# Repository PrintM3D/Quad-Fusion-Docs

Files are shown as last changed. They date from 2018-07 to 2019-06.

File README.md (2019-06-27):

# Welcome

                                                                                                                                                                                                                                                                                                                                                                                                                                                                                                                                                                                                                                                                               Welcome to the User Manual for the the QuadFusion print head.  This manual is hosted in GitHub.com and managed via GitBook.com.  Please feel free to add suggestions to any of the guides by creating a pull request or issue on [GitHub](https://github.com/PrintM3D/Quad-Fusion-Docs/issues).

NEW - July 2019 WalkThrough / Crash Course: For users setting up their quad head for the first time and looking to gain a deep understanding of the system to get the best results, start [here](https://coda.io/d/M3D-Official-Troubleshooting-Self-Help-Guide_dzE73kMbIAL/Quad-Expert-Crash-Course_sudLH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).

Steps/mm: For users setting up QuadFusion heads on their own system, important information can be found [here](getting-started/updating-control-board-settings.md).

**This user manual is a work in progress and may contain incomplete or incorrect information.  Please exercise caution with the information contained herein.  This message will be removed as the guide matures.**

If you are a complete beginner to 3D printing, please start at the [Beginner Guides](beginner-guides/).

If you are a more experienced 3D printer user, [Get Started Here](https://m3d.gitbook.io/m3d-quadfusion-documentation/getting-started).  This guide will get you set-up and walk you through your first print.

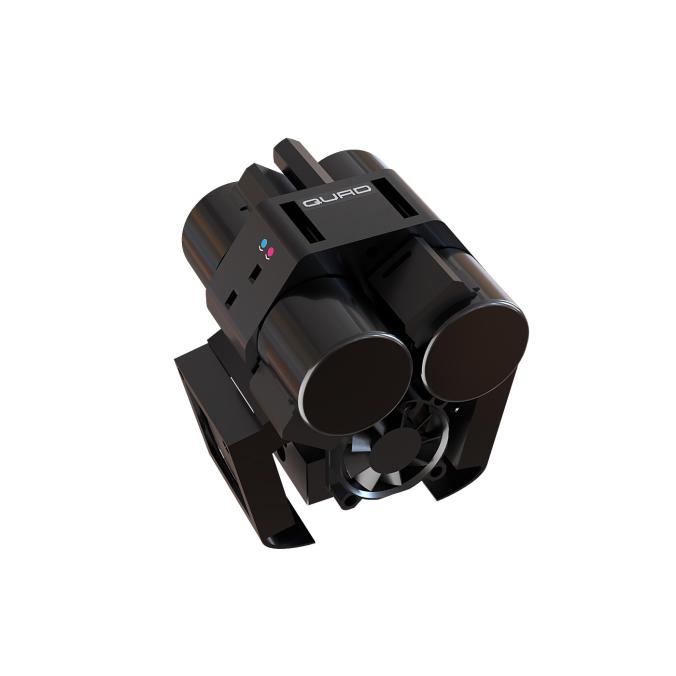
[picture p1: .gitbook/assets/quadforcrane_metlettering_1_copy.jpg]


## Contributing

The main way to collaborate to the guides is to become a collaborator.  But sometimes you simply want to submit a small contribution, without becoming a regular collaborator.

On GitHub, one can use the popular _Pull Request_ feature.  To do so, you would clone [https://github.com/PrintM3D/Quad-Fusion-Docs](https://github.com/PrintM3D/Quad-Fusion-Docs), make changes on your own copy, and submit back your changes by submitting a _Pull Request_ to M3D.  Then we will review the changes accordingly.

Thank you!

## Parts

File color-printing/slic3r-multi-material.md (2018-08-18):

# Slic3r Multi-Material

{% hint style="info" %}
Support for multi-color printing in common slicers is often limited to specific purposes or capabilities.  In this guide, we use Slic3r Prusa Edition and an M3D-developed script to make the generated G-Code compatible with a QuadFusion-enabled printer.  As slicer capabilities improve, this guide will be updated and the process will be simplified.
{% endhint %}

## You Will Need

Slic3r Prusa Edition \(link\)

NOTE: have been using 1.39.1

M3D Cleanup Script \(link\)

IPython Notebook or equivalent, such as Jupyter Notebook \(link\)

## Find \(or Create\) Multi-Part STL Set

## 

## Slice and Export

#### Load and Adjust Print Settings

#### Assign Tool Numbers

## Manual Cleanup Step

## Automated Cleanup Script

Take the .gcode file from the prior step and move it to your IPython working folder.  For example, on my system, these files are held in ~/Documents/Workspaces/\_python.  For this example, I moved the file "ed\_MAN1\_tower-of-cascades.gcode" to ~/Documents/Workspaces/\_python/Working.  \("Working" has been a convenient folder to hold the .gcode files separate from the actual IPython script file\(s\).\)

Launch IPython Notebook and load the script titled "PostprocSPEForColor4\_auto.ipynb".

Run the first three blocks of code.  \(The first is a short block defining "clamp" and nothing else; the next are much longer.\)

In the fourth code block, there is a note on values you will need to change for your particular job.  Adjust these values to your particular job.  First layer and other layer height are from your slicer setup.  The in file is the file you created in the prior step.  The out file is the .gcode file that will be created by the cleanup script and sent to the printer.

A large number of diagnostics messages will output when this code block is run.

TODO: in main -- find "def main\(\):"

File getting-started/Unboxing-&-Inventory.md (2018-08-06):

---
description: >-
  Included in the QuadFusion 3D Print Head package you will find a 3 fan mounts,
  3 fan guides, fasteners and cables. You will also find a sticker indicating
  the version shipped.
---

# Unboxing & Inventory

## Assembling the QuadFusion 3D Print Head

The QuadFusion 3D Print Head needs to be assembled before you can mount it to your printer.  Please follow these steps to complete the assembly

1. Attach the fan mounts to the QuadFusion:

    2. Attach the fan guides to the fans:

    3. Attach the fans to the fan mounts:

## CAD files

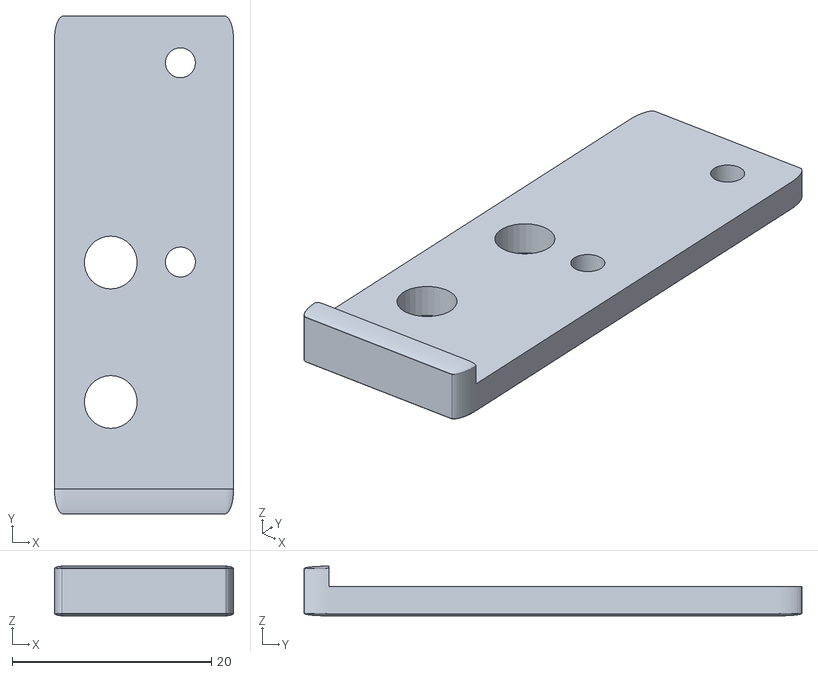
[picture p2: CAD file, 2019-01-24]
.gitbook/assets/cr10s_quad_stencil.stl
18.0 x 50.0 x 5.00

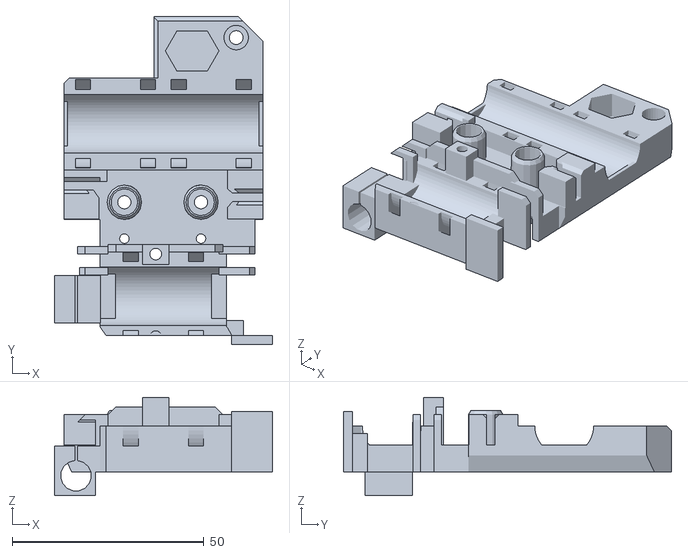
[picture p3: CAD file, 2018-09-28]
.gitbook/assets/prusa_quad_mount.STL
57.0 x 85.6 x 25.7

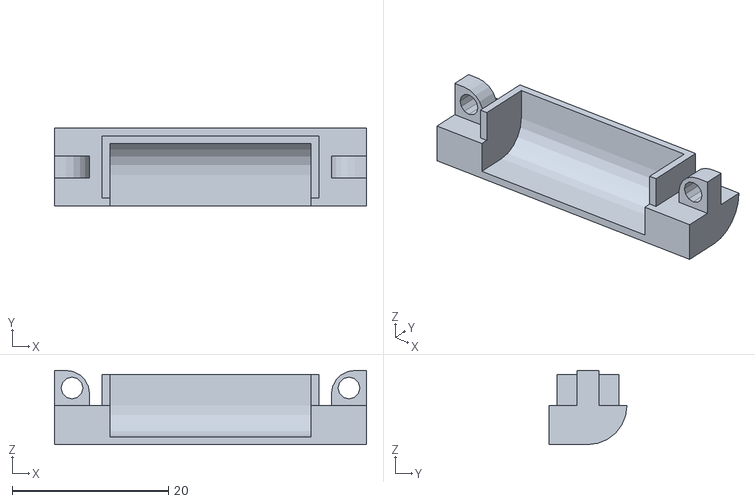
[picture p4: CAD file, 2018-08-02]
.gitbook/assets/quad-nozzle-fan-duct-v1.0.STL
40.0 x 10.0 x 9.50

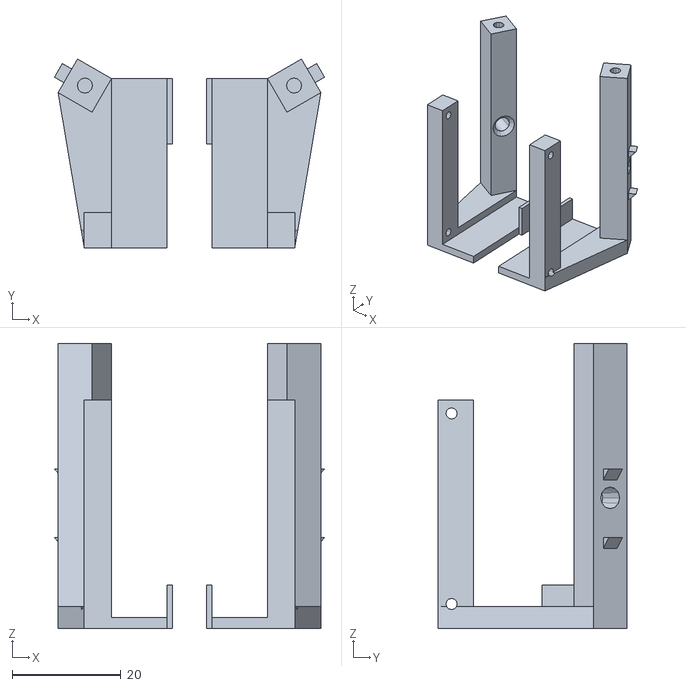
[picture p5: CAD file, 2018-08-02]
.gitbook/assets/quad-fan-mount-2-v1.1.STL
49.6 x 34.7 x 52.4

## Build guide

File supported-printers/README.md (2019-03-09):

# Printer Installation

The QuadFusion is a versatile 3D print head, so it is very likely that it will be able to adapt to whatever printer you have at home. At M3D we have mounted the QuadFusion on many different types of printers. The following guides will show you how we attached the QuadFusion not only mechanically, but electrically as well.

{% hint style="info" %}
The QuadFusion is compatible with most 3D printers, including those not listed here!
{% endhint %}

{% hint style="warning" %}
**Disclaimer: Some of the printers listed are NOT M3D products. We would like to make it clear that we have no affiliation with these printers or the companies that made them.**
{% endhint %}

{% page-ref page="m3d-crane.md" %}

{% page-ref page="m3d-promega.md" %}

{% page-ref page="cr-10s.md" %}

{% page-ref page="prusa-i3-mk2s.md" %}

{% page-ref page="duet-maestro-wiring.md" %}

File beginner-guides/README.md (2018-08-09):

# Beginner Guides

This chapter serves as an introduction to 3D printers for Quad Fusion 3D Print Head users who are not familiar with 3D printing. You will find numerous guides that explain fundamental 3D printing concepts from the start. Experienced 3D printer users are welcome too! You never know what information you might find in this chapter. If you are a more experienced 3D printer user, please follow the [Getting Started](../getting-started/) chapter.

{% page-ref page="beginner-preparation.md" %}

{% page-ref page="beginner-moving-the-motors.md" %}

{% page-ref page="beginner-introduction-to-g-code-commands.md" %}

{% page-ref page="beginner-software-layers.md" %}

{% page-ref page="beginner-what-is-slicing.md" %}

{% page-ref page="beginner-printing-the-print.md" %}

{% page-ref page="beginner-where-to-go-from-here.md" %}

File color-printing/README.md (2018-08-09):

# Color Printing

This guide aims to help with color printing using the QuadFusion.

{% page-ref page="setting-up.md" %}

{% page-ref page="slic3r-multi-material.md" %}

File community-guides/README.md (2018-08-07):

---
description: This section will host awesome guides made by our community.
---

# Community Guides

This page serves as a future place for community guides. If you have a great idea, procedure or guide that you want to share. Create a pull request on the [M3D QuadFusion Docs repository](https://github.com/PrintM3D/Crane-Docs). **\(Change URL\)**

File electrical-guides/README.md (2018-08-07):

# Electrical Guides

This chapter contains guides that explain the wiring of components of the QuadFusion.

{% page-ref page="../supported-printers/duet-maestro-wiring.md" %}

{% page-ref page="the-electrical-standard.md" %}

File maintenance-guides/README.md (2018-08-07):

# Maintenance Guides

This chapter contains guides that explain how to preform maintenance on the QuadFusion.

{% page-ref page="screw-and-tool-list.md" %}

{% page-ref page="temperature-calibration.md" %}

{% page-ref page="changing-nozzles.md" %}

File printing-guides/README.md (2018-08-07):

# Printing Guides

This chapter contains guides that explains printing with the QuadFusion.

{% page-ref page="slicers-and-printer-settings.md" %}

{% page-ref page="heating-and-temp-sensor.md" %}

{% page-ref page="loading-and-unloading-filament.md" %}

{% page-ref page="filament-success-guide/" %}

{% page-ref page="filament-extrusion-rate.md" %}

{% page-ref page="tool-definitions.md" %}

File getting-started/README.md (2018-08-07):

# Getting Started

Follow the guides in this Getting Started chapter of the QuadFusion 3D Print Head Docs to properly configure your printer and start printing!

## Table of Contents

{% page-ref page="critical-warnings-and-information.md" %}

{% page-ref page="unboxing-and-inventory.md" %}

{% page-ref page="getting-connected.md" %}

{% page-ref page="updating-firmware.md" %}

{% page-ref page="updating-control-board-settings.md" %}

{% page-ref page="homing-the-printer.md" %}

{% page-ref page="first-print.md" %}

{% page-ref page="getting-started-where-to-go-from-here.md" %}

* [Critical Warnings & Information](critical-warnings-and-information.md): Contains important warnings and information about using the QuadFusion.
* [Unboxing & Assembly](./): A step-by-step guide to unbox your QuadFusion and assemble the shipped components.
* [Getting Connected](getting-connected.md): A generic guide to setting up your QuadFusion.
* [Updating Firmware](updating-firmware.md): A walk through on how to update your Duet Maestro's firmware.
* [Updating your Control Board Settings](updating-control-board-settings.md): Contains important information to understand the specs on you QuadFusion.
* [Changing Homing Offsets](homing-the-printer.md): A guide that goes through the new offsets for your QuadFusion. 
* [First Print](first-print.md): A guide that helps you print a simple print to check setup.
* [Getting Started: Where to Go From Here](getting-started-where-to-go-from-here.md)

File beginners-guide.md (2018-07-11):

# Beginners Guide

WORK IN PROGRESS!

This guide provides a supplement of information to the [Getting Started](https://m3d.gitbook.io/promega-docs/getting-started) Chapter. This guide serves as an introduction to 3D printing and the Promega for new 3D printer users. Follow this guide from start to finish in order to gain a better understanding of the fundamental concepts of a 3D printer and the Promega! If you are more familiar with 3D printing or similar concepts feel free to continue on to other guides!

## Network Setup

1. Complete the [Network Setup](https://m3d.gitbook.io/promega-docs/getting-started/network-setup) guide. This will allow you to connect to the Duet Web Console on the Duet Maestro, the control board of the Promega \(pictured below\). The Duet Web Console is a web interface that allows you to control the Promega in a much easier manner. The second image below shows the homepage of the Duet Web Console.

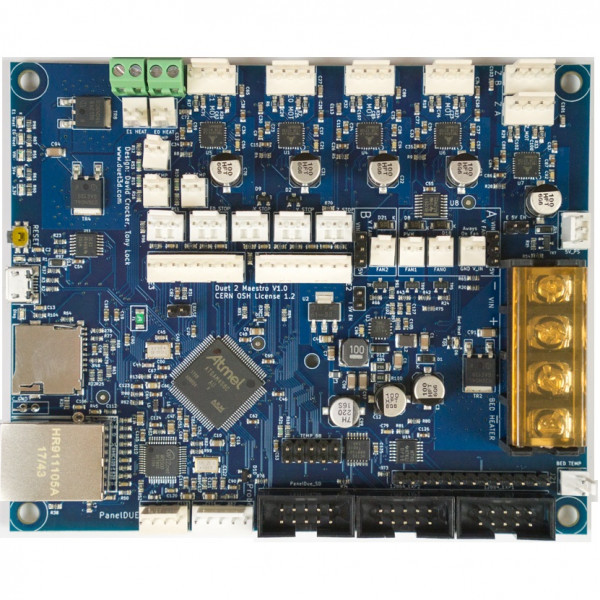
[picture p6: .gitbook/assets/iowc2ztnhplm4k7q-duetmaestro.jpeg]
   

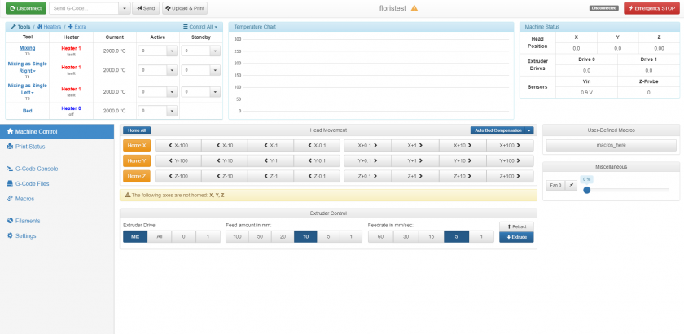
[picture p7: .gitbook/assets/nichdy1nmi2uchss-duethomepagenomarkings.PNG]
   

## Printer Assemblies

This guide will cover a significant amount of technical knowledge and terms. The different assemblies of the Promega will be mentioned frequently in the sections below.

List of Promega Assemblies:

* **Extruder Assembly**: This heats up and prints the filament. It is also referred to as the extruder carriage.
* **CoreXY Assembly**: A belt system that allows the extruder carriage to travel on a plane.
* **Z-platform**: A heated bed that is actuated up and down with belts.

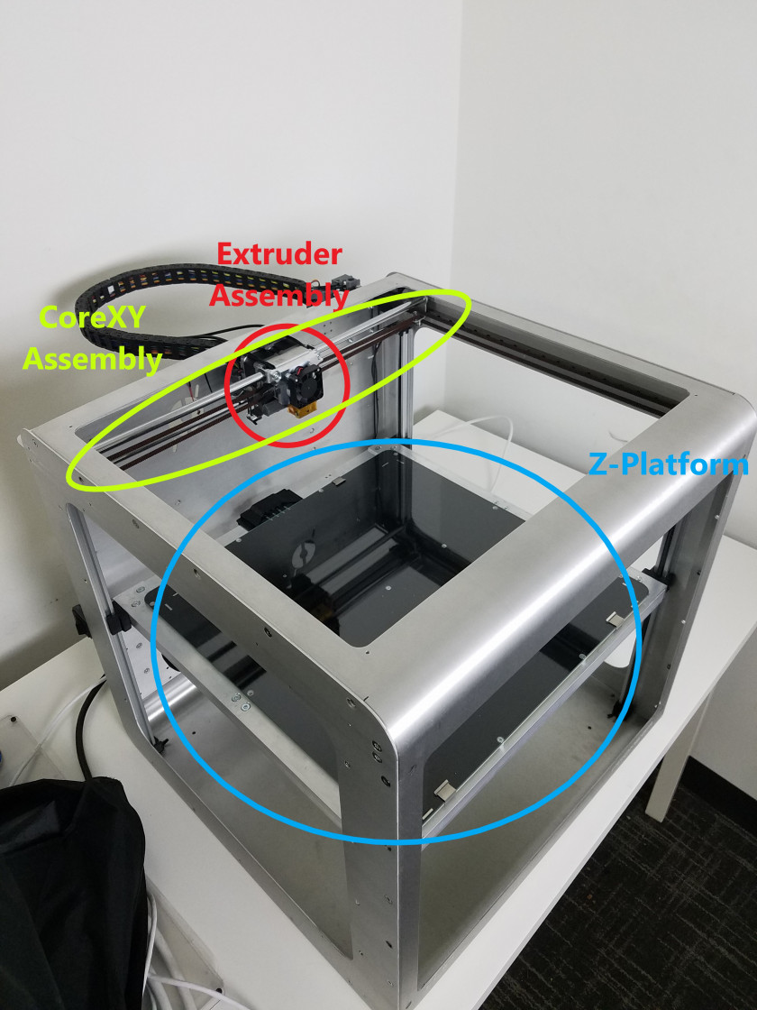
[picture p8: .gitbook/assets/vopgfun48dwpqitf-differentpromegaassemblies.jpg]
  

## Printer Coordinates

In your math classes you have probably heard the term: _Cartesian Coordinates_. This intimidating term is not as bad as it sounds. It refers to the 3D coordinate system that is used almost every where, including the Promega. It features three different axes \(X, Y and Z\), all perpendicular to each other, as seen in the image below. The origin of the cartesian system is located at the intersection of the three different coordinate axes. At this point, the X, Y and Z position are all zero.

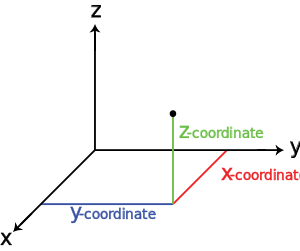
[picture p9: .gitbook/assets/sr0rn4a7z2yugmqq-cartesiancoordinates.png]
Cartesian Coordinates


In the case of the Promega, the cartesian coordinate frame is used to track the location of the nozzle. The nozzle can be considered a point that can be moved along the X, Y and Z axes in the printer. The nozzle is moved in the X and Y directions with a coreXY belt system and in the Z-direction with the z-platform. The orientation of the cartesian coordinate frame is not the same as in the image below. Look below to see the cartesian coordinate frame in the Promega.

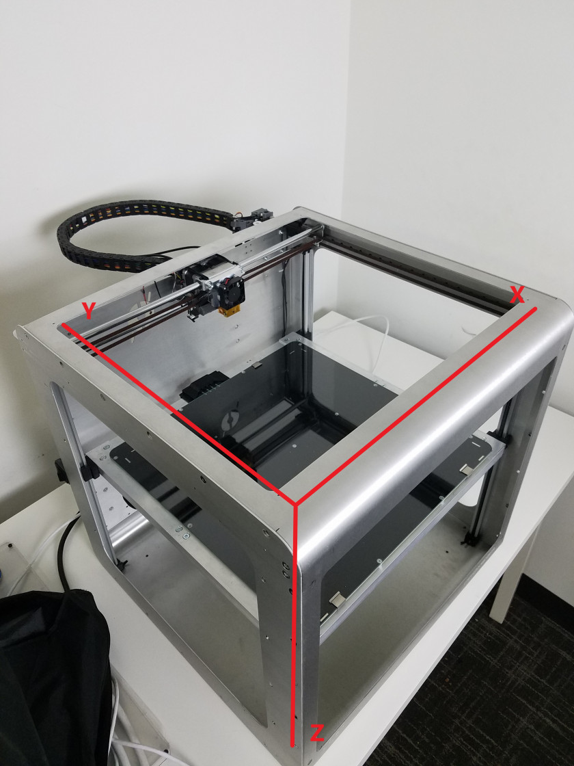
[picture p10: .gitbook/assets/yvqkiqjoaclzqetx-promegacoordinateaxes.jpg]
Promega Coordinate Axes


**The Origin**

The origin of the Promega is located at the front-top-left corner of the printer, where the three red lines intersect. If the printer moves to X0, Y0 and Z0, or \(0,0,0\) it will end up in this corner. The position of the nozzle of the printer is measured from this point. As mentioned before, the printer moves in the X and Y direction with the a coreXY belt system, which we will go over later. The Z-axis works differently, instead of moving the nozzle away from the bed, the Promega moves the bed away from the nozzle. The nozzle is always located on a single plane which it can be moved across by the coreXY system. The Z-axis distance value increases as you move the bed **down**, away from the nozzle, and the distance decreases as you move the bed **up**, toward the nozzle. This might be counter-intuitive at first, as a normal oriented cartesian coordinate frame will have the Z-axis pointing up, but you will get used to it quickly.

**Coordinate Units**

The Promega 3D printer uses millimeters as units. All the commands given to the printer will be in millimeters. For example, if you told the printer to go to \(200, 380, 150\) or 200 mm in the X direction, 380 mm in the Y direction and 150 mm in the Z direction it might look something like in the image below. The distances are measured from the origin of the Promega, depicted by the circle in the image below.

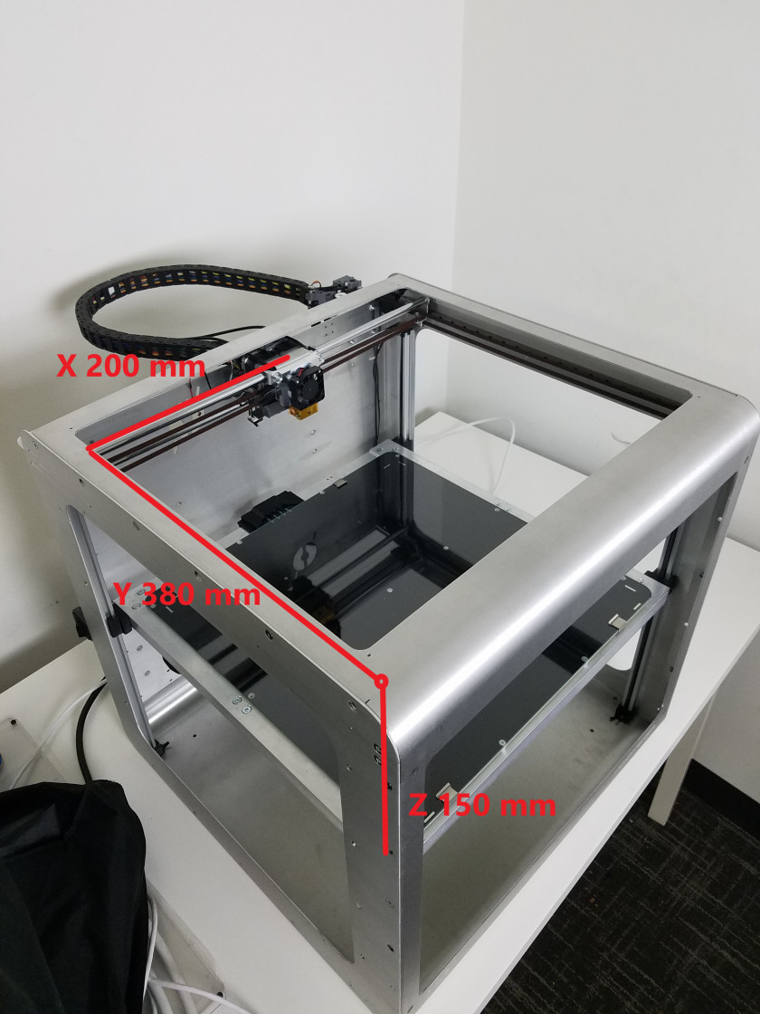
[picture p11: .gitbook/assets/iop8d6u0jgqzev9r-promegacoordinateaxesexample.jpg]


**Machine Status**

The Duet control board will keep track of its current position relative to its origin. Again, the origin is where the X, Y and Z position of the 3D printer are 0. The position of the printer can be found in the Duet Web Console on the top-right in a table labeled _Machine Status_. This can be seen in the image below where the printer displays a position of 300 mm in the X-direction and 300 mm in the Y-direction and 159.1 mm in the Z-direction. Remember that this is all relative to the origin of the printer.

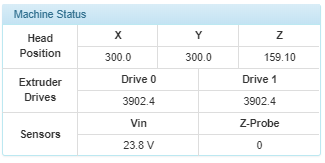
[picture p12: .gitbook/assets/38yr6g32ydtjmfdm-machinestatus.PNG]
Duet Web Console Machine Status Table


**Homing**

The origin of the printer can change as well, as shown in the images above, it is usually in the top-front-right corner, but only after you home the printer. Homing the printer, which will be covered later, will send the printer to the limit switches and update the position of the printer. Whenever you start the printer, the printer will reset its previous position and label its current position as \(0,0,0\). This means that the position where you power on your printer is \(0,0,0\) is considered the origin, until you home the printer. Therefore, **it is very important to home the printer once you switch on the printer.** Keep track of the _Machine Status_ table on the Duet Web Console to see where the printer thinks it currently is located.

**Moving the Motors**

Before you power on your motors you can manually move the extruder head around the printer. Follow the steps below in order to start moving the printer.

1. Move the extruder head to the center of the printer by hand. This should not take a lot of effort to do as long as the motors are not powered. Once you move the motors, the motors will be powered and resist any force acted on them.
2. Go to the _Machine Control_ tab of the Duet Web Console.

Machine Control Tab in Duet Web Console

1. Press _Home All_, this will home all the axes of the printer and ensure that the origin of the printer is located at the front-top-left corner of the 3D printer. After the homing process is complete, you can see that the position of the 3D printer is updated in the _Machine Status_ tab on the Duet Web Console.
2. Press the X-10 button in the _Head Movement_ window. This will move the extruder carriage of the printer 10mm in the negative X direction, this should be towards the left if you are facing the front of the printer. Now press the Y-10 button, this will move the printer -10 mm in the Y-direction. If you are facing the front of the printer, this should send the extruder carriage towards you. You can also press the Z buttons, but remember that the bed is all the way down and resting on the limit switch after the homing process. You will have to move the bed in the negative Z direction in order to move it up. Press the Z-10 button in order to move the bed up 10 mm.
3. You can keep pressing the buttons to move the extruder carriage to become more familiar with the directions and coordinate system of the Promega.

**Absolute vs. Relative**

A 3D printer movement allows for two different modes, absolute and relative. These two terms are also used frequently in machining and other engineering processes. Absolute describes a position or command with respect to the origin or zero position. Relative describes the position of a 3D printer relative to the previous point. For example, if you tell the printer to move \(20,20,20\). Absolute mode will send the printer to the point where X = 20mm, Y = 20mm and Z = 20mm. While relative will send the printer 20 mm in the X-direction, Y-direction and Z-direction relative to its previous position. This means your printer will go to two completely different places depending on if you are in relative or absolute mode.

## G-Code Commands

Now that you are familiar with the coordinate system of the Promega, its orientation and direction, we can get started with learning and sending G-code commands. G-code commands are sent one line at a time, with one command per line. When you send a print file to your printer in order to print something, you are sending the printer a long list of G-code commands. It will look something like this \(but way longer!\):

```text
G1 X173.448 Y182.05 E0.03872
G1 X173.922 Y181.843 E0.03871
G1 X174.422 Y181.712 E0.03868
G1 X174.883 Y181.662 E0.0347
G1 X178.301 Y181.524 E0.256
G1 X183.787 Y181.051 E0.41207
G1 X189.186 Y180.278 E0.40816
G1 X194.553 Y179.196 E0.40972
G1 X197.18 Y178.55 E0.20245
G1 X202.457 Y177.012 E0.41134
G1 X208.239 Y174.993 E0.45832
G1 X208.864 Y174.84 E0.04815
G1 X209.841 Y174.699 E0.07387
G1 X210.32 Y174.665 E0.03594
G1 X240.74 Y174.665 E2.27649
G1 X241.414 Y174.733 E0.0507
G1 X242.865 Y175.031 E0.11085
G1 X243.362 Y175.174 E0.0387
G1 X243.641 Y175.293 E0.0227
G1 X244.676 Y175.79 E0.08592
G1 X245.287 Y176.169 E0.05381
G1 X245.992 Y176.719 E0.06691
G1 X246.435 Y177.134 E0.04543
G1 X247.028 Y177.801 E0.06679
G1 X247.379 Y178.274 E0.04408
G1 X247.842 Y179.028 E0.06621
G1 X248.113 Y179.576 E0.04575
G1 X248.46 Y180.476 E0.07218
G1 X248.633 Y181.098 E0.04831
G1 X248.792 Y181.998 E0.06839
G1 X248.843 Y182.581 E0.0438
```

**Basic Commands**

The command, `G1`, you are see above is called the move command. This is arguably the most important G-code as it allows you to move the printer. Each G-code command consists of a letter followed by a number. `G31`, `M564` and `T0` are all valid G-code commands as well. The Duet Maestro control board runs [RepRap Firmware](https://reprap.org/wiki/RepRap_Firmware). This firmware determines what commands are valid, and which commands are not. You can find all the valid commands that you can send in a long list on the [RepRap Wiki G-codes Page](https://reprap.org/wiki/G-code). After the initial letter-number combination of the G-code command a parameter can follow. This is also visible with the G-code commands listed above, the command `G1 X248.843 Y182.581 E0.0438` has `X248.843 Y182.581 E0.0438` as parameters. Many different G-code commands have optional parameters that can be entered after the initial command.

**Absolute vs. Relative in Commands**

With the `G1` command you can move the printer. However, where the `G1` command moves your printer depends on whether you are in absolute or relative mode. Absolute mode is enabled whenever you send the command `G90`, relative mode is enabled when you send the command `G91`. Whenever you are printing absolute mode is typically enabled. If you restart your printer, absolute mode will also be enabled. If you send the command `G1 X150 Y120 Z100` in absolute mode \(`G90`\), the printer will move to the position X = 150mm, Y = 120mm and Z = 100mm, **relative to the origin**. If you send the same command in relative mode \(`G91`\), it will send the printer 150 mm in the positive X-direction, 120 mm in the positive Y-direction and 100 mm in the Z-direction relative to where the printer currently is positioned. The same command can send the printer to two completely different places depending on what mode you are in. As you saw in one of the commands above, the move command, `G1`, can also have an `E` parameter, this allows for a movement of the extruder motor.

**Feedrate**

Aside from the `X`, `Y`, `Z` and `E` parameters which allow the printer to move each of the motors, there is one other important parameter `F`. `F` is the feedrate of the motor, or is simple terms, the speed that the motor will travel at. The units of the `X`, `Y`, `Z` and `E` parameters is mm. However for `F` or feedrate the units are `mm/min`. A normal travel feedrate \(speed\) would be 3000mm/min, but for printing the feedrates are typically much lower.

**The Movement Buttons**

In one of the steps above you used the buttons in _Machine Control_ to move the printer. What is really happening here is that when you press a button a list of G-code commands are sent to the printer. For example, if you press the X+10 button to move the printer 10mm in the positive X-direction this is what is actually sent:

```text
M120
G91
G1 X10 F6000
M121
```

You might be familiar with two of the G-code commands here `G91` and `G1`. `G91` enables relative mode, so the next move command that is sent will be with respect to the printers current position and not the origin. After the `G91` command, the move command `G1` is sent. This sends the printer 10mm in the positive X-direction at a feedrate of 6000mm/min. The `M120` and `M121` commands are stack push and pop. If you are not familiar with these two programming terms, then don't worry, they are not important to know for a beginning user. All you have to know is that it will disable relative mode `G91` and return to absolute mode `G90`. This is because you want the printer to be back in absolute mode after pressing the move buttons.

**Sending G-code Commands**

Now that you are more familiar with G-code commands you can try to complete the steps below in order to see how the printer responds to you sending G-code commands directly to the printer itself.

1. Find the _G-code Console_ tab in the Duet Web Console. 

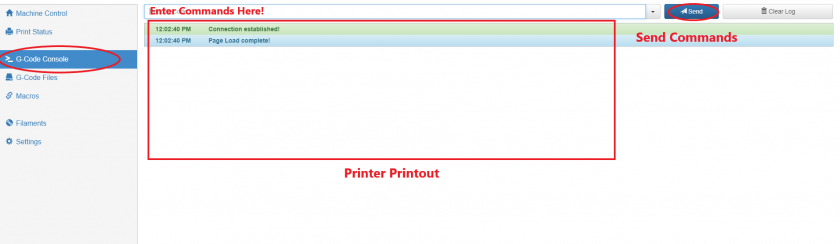
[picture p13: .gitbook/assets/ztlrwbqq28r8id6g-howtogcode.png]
G-Code Console in the Duet Web Console


1. This tab allows you to send commands to the printer using the textfield as seen above. Once you enter a command in the text field you can press _Enter_ or press the dark-blue send button. The printer will then process the command and execute it. If the command executed successfully you will see a print out of the command you send in the _Printer Printout_ terminal with a green background. If the firmware encountered an error while trying to process the command, it will printout the command with a red background and more information about the error. 3. This step assumes you have the printer homed from the previous steps. If you have not yet homed your printer, click the _Home All_ button in the _Machine Control_ tab. Try sending the command `G1 X200 Y200`. This will move the printer to 200 mm X and 200 mm Y. Send the command `G1 Z150`. This will move the bed to about 150 mm from the nozzle. 4. You can keep sending commands to move the printer around the buildspace. The table below represents the limits of the printer, the firmware should prevent you from going past these limits. Still, try to keep your move commands within the buildspace of the printer. You can also try to change the feedrate of the printer to see how the speed of the printer changes as the printer moves around.

|  | Axes Limits |  |
| --- | --- | --- |
|  | Max \(mm\) | Min \(mm\) |
| X - Axis | 388 | 0 |
| Y - Axis | 388 | 0 |
| Z - Axis | 377 | 0 |

**Other G-code Commands**

Of course there are many more RepRap supported G-code commands \(as you might have seen on the [RepRap Wiki](https://reprap.org/wiki/G-code)\). You will come across some of them as you follow this guide. Whenever you have questions about what a command does, you can look up the command on the wiki.

Throughout the different guides you will find G-code in `this format`. That typically means you can execute the G-code command. Comments are denoted by any text following a semi-colon ";". A new line will end the comment.

`G1 X100 ; This is a comment!`

## The Extruder

Next, we will move on to one of the most important assemblies on the Promega, the extruder! This complicated assembly can reach temperatures above 300°C in order to melt plastic and print it. The extruder assembly contains a fan directly on the front, this is called the _Cold-Section Fan_. It is meant to keep the extruder block, directly behind it, cold. If the extruder block gets too hot, the filament could start melting before the filament ever reaches the nozzle. On the underside of the extruder assembly, there are two smaller fans called _Nozzle Fans_. These are meant to call any filament that is pushed out of the nozzle so that it immediately becomes rigid. On the right of the nozzle fans is a small electronics board called the _IR Probe_. This probe uses Infra-Red rays in order to detect the bed. On the left of the extruder is a small deploy-able limit switch, this is also a Z-probe. Z-probes are used in order to measure the exact distance from the nozzle to the bed. They are also used in order to level the bed of the printer as printing requires a very flat and level surface. You can view the image below to see a diagram of the different extruder components.

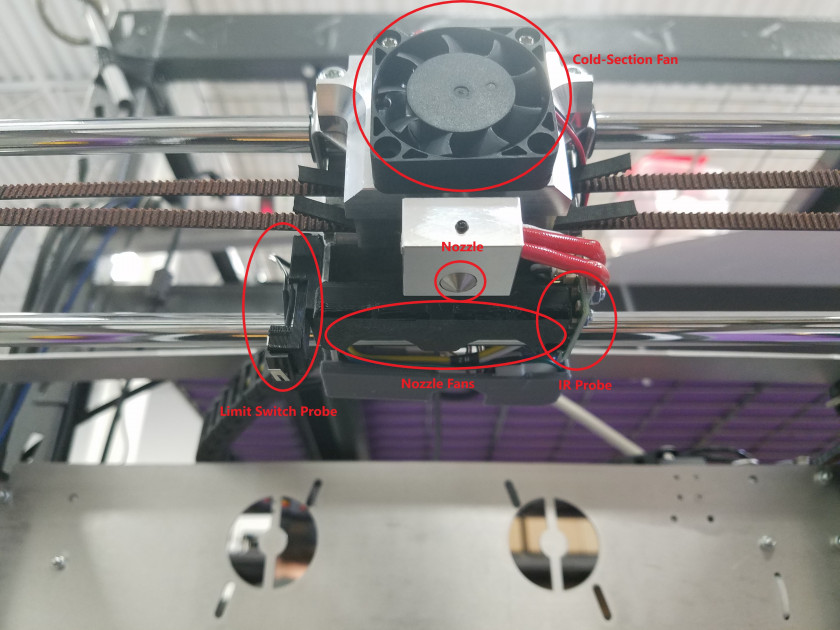
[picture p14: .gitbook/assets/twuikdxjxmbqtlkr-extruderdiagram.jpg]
Extruder Diagram


### Tools

Tools are a relatively new concept in 3D printing. They allow you to create different extruder configuration ahead of time that you can quickly switch between while printing. The Duet Maestro board uses tools in order to allow printing with multiple extruders, or mixing extruders. The Promega actively makes use of this in order to print with different tool mixing ratios, or do dual nozzle prints with the K'tana. You can find your currently configured tools in the Duet Web Console in a table labeled: _Tools/Heaters/Extra_ on the top-left.

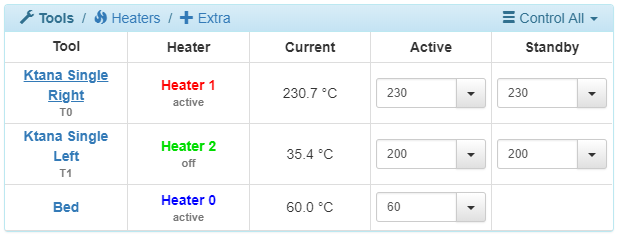
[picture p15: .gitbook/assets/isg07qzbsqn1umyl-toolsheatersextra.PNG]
Tools &amp; Heaters


In the image above there are two different tools. In RepRap firmware, tools are defined as `Tnnn`, where `nnn` represents a tool number. In the image above there are tools T0 and T1. Each tool has it's own extruder motor attached to it, or multiple if you are mixing. A tool also has one heater attached to it. All these tools are defined and configured when the printer powers up with G-code commands, we will go over how exactly that works later. Below are the default tools for the Compound and K'Tana setups. In order to select a tool you can either click on the tool name in the Duet Web Console or you can send the command `Tnnn` where `nnn` represents the tool number. If you wanted to switch to tool 0, you would send the command `T0`. The Duet Web Console always shows you which tool is selected: it will underline the tool name. In the image above T0 is selected.

Compound Tools:

* `T0`: Mixing tool
  * Extruder 0 \(Left\) & Extruder 1 \(Right\)
  * Heater 2
  * Allows for extruding two filaments and combining them at a 1:1 ratio
* `T1`: Single Left
  * Extruder 0 \(Left\)
  * Heater 2
  * Extrudes with only the right extruder
* `T2`: Single Right
  * Extruder 1 \(Right\)
  * Heater 2
  * Extrudes with only the left extruder

K'Tana Tools:

* `T0`: K'tana Single Right
  * Extruder 1 \(Right\)
  * Heater 1
* `T1`: K'tana Single Left
  * Extruder 0 \(Left\)
  * Heater 2

In the future, if you find that none of your extruders are working, or an extruder you didn't expect to be running is running, chances are you have the wrong tool selected. Use the `Tnnn` command in order to select a tool with number `nnn`.

### Filament Properties

There are many different filament types used in the 3D printing industry, a [Google search](https://www.google.com/search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) will prove that. They vary in material, diameter and many other properties. The Promega allows you to print with 1.75mm diameter filament. The Promega can also print many different materials, but if you are a beginner we recommend ABS-R or PLA. These two materials tend to be easiest to print with. PLA prints well at around 200°C and ABS-R at 230°C. Printing temperature varies greatly depending on what material you are printing with. Please do appropriate research before attempting to extrude a new filament. Follow the section below in order to get started with extruding.

### Loading Filament

To load filament into the extruder you will need to find two small holes on the top of the extruder assembly. 1.75mm diameter filament can be loaded into this opening. It will then be grabbed by the extruder motor and pushed down into the hot-end. The hot-end term refers to the pieces of the extruder which will heat up in order to melt the plastic. In the Promega's case that is the nozzle and the aluminum block surrounding it. Once the filament is melted in the hot-end it will come out of the nozzle. The compound nozzle will have two holes to allow entry to two different filaments. It then melts both filaments and combines them to produce one stream of filament coming out. The K'Tana has two different nozzles and therefore each filament will get extruded out of separate nozzles. To load filament follow the steps below.

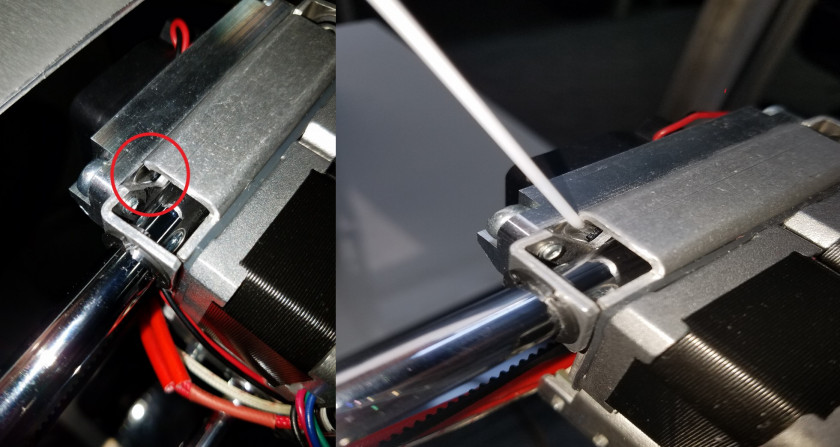
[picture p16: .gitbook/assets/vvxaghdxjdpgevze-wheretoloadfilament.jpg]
Where to Load Filament in the Extruder


1. To load filament into the extruder you will first have to heat up the nozzle. It also helps to have the extruder located in the center of the printer. So move the extruder to the center of the printer by entering the command `G1 X200 Y200`.
2. There are multiple ways to heat up the nozzle to your desired temperature. One is with a G-code command and the other is with the Duet Web Console. Heating up tools with the Duet Web Console is the easiest. In the table _Tools/Heaters/Extra_ on the Duet Web Console, enter the desired temperature in the circled box below \(your _Current_ reading should not have a value of 2000°C, 2000°C is an error value\). Once you have entered the temperature press Enter. You should now see a steady rise in temperature in the _Current_ box and on the graph to the right. The temperature you set should depend on the filament you are planning to extrude.

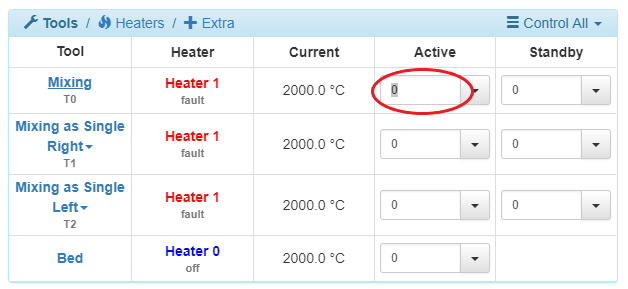
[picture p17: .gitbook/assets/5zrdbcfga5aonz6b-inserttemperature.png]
   

3. Once the extruder has reached it's set temperature you are ready to load your filament. Take the filament and insert it into the opening circled in red in the image above. If you are attempting to extrude with a Compound nozzle, you will have to load filament into both openings in the extruder. For the K'Tana you will only have to load filament on one side. Now, on the Duet Web Console go to the _Machine Control_ tab in order to move the extruder motors. In this tab there is a box called _Extruder Control_. Here you can select the extruder you want to control and how much filament you want to extrude and at what speed. If you have the Compound nozzle, set the _Extruder Drive_ settings to _Mix_ in order to get both extruder motors to push filament. If you have the K'Tana, select Drive 0 or 1 depending on which side you loaded filament into. The _Feedrate amount_ should be set to 10mm and the _Feedrate_ to 5mm/sec. You can then press _Extrude_ this should move the filament into the extruder. It could be possible that you have to push the filament properly into the opening until the extruder grabs it.

   

4. Once the filament is inside the extruder keep pressing _Extrude_ until filament comes out of the nozzle. You can increase the _Feed amount_ to 50mm or more to decrease the times you have to press _Extrude_.
5. Congratulations, you have just created your first print! It probably looks like a long stream of filament, but that counts, right? You can keep pressing the _Extrude_ button for as long as you like, or you can move on to the next section.

### Extruding with G-code Commands

The steps that you accomplished above in order to extrude filament can also be done with G-code commands. Follow the steps below in order to learn more G-code commands.

1. Select your appropriate tool with `Tnnn`. For example, tool 0 with `T0`.
2. Turn off the heat to your tool by sending the command `G10 Pnnn S0`. `G10` allows you to set a tool temperature. The `P` parameter and `nnn` represents your tool number that you want to change the temperature of. `Snnn` is the temperature of the tool. So by setting the temperature to 0 the tool is turned off.
3. If you wanted to turn the temperature of a tool back on you would have to enter the command `G10 P0 Snnn` where `nnn` is your new tool temperature. The `G10` `S` parameter only sets the **active** temperature of a tool. This means the tool will only go to that temperature when it is selected or active.
4. If you wanted to extrude 100mm of filament at a feedrate of 20 mm/sec you could enter the commands below. Remember that you should zero your extruder first before telling your extruder to move. This is because your extruder could have a very high position in mm, for example 10291mm. If you then tell the extruder to move to the absolute position of 100mm. The extruder will have to travel 10191mm backwards, and that will take a long time! You can also turn on relative extruder moves with `M83`, and then you would not have to zero the extruder as it just adds 100mm to the position the extruder is already at.

   ```text
   G92 E0
   G1 E100 F120 ; Remember that Feedrate is in terms of mm/min!
   G92 E0
   ```

   ```text
   M83 
   G1 E100 F120
   M82
   ```

5. To retract, pull filament back into the extruder, send a negative extruder position. Like `G1 E-100 F3000`.

### Alternative Commands to Heat

Throughout your printing career with the Promega you will notice other commands to heat up your nozzle. `M104` and `M105` can also be used to heat up your tools.

`M104 Snnn`: Heat up your active tool to `nnn`°C.

`M109 Snnn`: Heat up your active tool to `nnn`°C and wait until temperature is achieved.

`M140 Snnn`: Heat up your bed to `nnn`°C.

`M190 Snnn`: Heat up your bed to `nnn`°C and wait until temperature is achieved.

## The Bed

The print bed is a very crucial piece on the Promega. When printing on a 3D printer it is important to have an even and level bed relative to your nozzle. This means that your print bed should not have bumps and should be parallel to the plane that the coreXY moves along. This is extremely hard to maintain across a print bed that is almost 400mm x 400mm! When you heat up your heated bed the bed will warp and your print surface will not be level or even. It is important to have a level bed because a 3D printer has to be able to get it's filament to stick to the bed. If the bed is 0.2mm too high the extruder will end up printing in air, and if the bed is 0.2mm too low the nozzle could crash into the bed. So the tolerances are extremely tight! There are multiple things you can do in order to ensure that your bed is as level as possible. First of all you can mechanically level your bed by skipping bed teeth. But this will only get you an accuracy of ~1mm, and that is not enough. Duet Firmware has a bed leveling compensation process that is supported. This is highly recommended for printing large prints! A heated bed is very important to prevent warping of a print and ease first layer adhesion to the build plate. A hot bed can prevent print warping as it keeps the temperature of the first layer at a consistent temperature. A warping print can peel off the heated bed and ruin your print.

### Z-probe Offset

As you might have read previously, the extruder assembly contains two Z-probes. The IR probe, located on the right of the extruder assembly and the Z-probe limit switch on the right side of the extruder. Both of these Z-probes serve the same purpose, zero-ing the Z-axis and leveling the bed. This beginners guide will cover only how to calibrate and use the Z-probe limit switch. The IR probe is recommended for more advanced users as it tends to be more noisy and inconsistent under the wrong conditions. The Z-probe limit switch is easier to produce consistent and reliable results with.

**The Limit Switch**

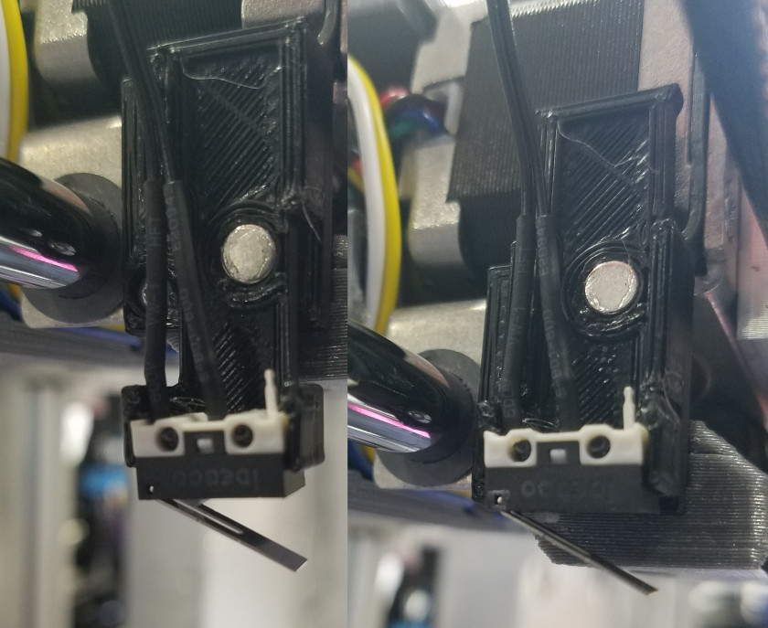
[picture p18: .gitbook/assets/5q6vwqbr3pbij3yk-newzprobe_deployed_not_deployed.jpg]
Z-Probe Deployed \(Left\) and Retracted \(Right\)


Z-probes are extremely useful to zero the Z-axis. This is because the Z-probes typically have a reliable and constant offset from the nozzle. Once you find that offset, you run a G-code command in order to ensure that your print will be successful. The limit switch Z-probe is simply an end-stop attached to a deployable 3D printed mount. In the picture above you can see the limit switch in the deployed state on the left and the non-deployed state on the right. Deploy the limit switch by pressing down on the 3D printed tab and retract the probe by pulling the switch up. It is important for the limit switch to be deployable because the limit switch needs to make contact with the bed whenever you are probing, but it should be out of the way whenever you are printing. Whenever you send the probe command `G30` the bed will move up toward the nozzle until the Z-probe is triggered. When the Z-probe is triggered, the Z-value of the printer is set to the Z-offset of the Z-probe. You can set the Z-offset of the Z-probe with the `G31` command and its parameters.

**Always deploy the switch before probing**. This is extremely important, otherwise you **will** crash the nozzle into the print bed as the Z-probe will never be triggered.

**Setting the Limit Switch Offset**

1. Home the printer again, just to ensure you do not crash the printer throughout this process.
2. Print head to the center of the build plate by sending the command `G1 X200 Y200`
3. Heat up the bed to the preferred printing temperature. You can do this by sending the command `M140 Snnn` where `nnn` is your temperature in °C. You can always look up the recommended bed temperatures for specific materials online. For PLA, a bed temperature of 50°C will work well. For ABS-R, a bed temperature of 60°C is recommended. 
4. Wait until the heated bed has reached temperature before continuing.
5. Set the Z-probe offset to 0 by entering the command `G31 G31 P999 X-40 Y28.5 Z0`. This will make it easier to gauge the distance between the Z-probe and the nozzle in the following steps.
6. Run the command `G29 S2`. This clears any active bed leveling compensation. This is **very** important as it will conflict with your updated Z-probe offset and induce a 0.1 - 0.3mm error depending on the magnitude of your bed leveling compensation at that point.
7. Deploy your Z-probe
8. Check whether the Z-probe is functioning correctly. This is a great step to perform before using your Z-probe in order to prevent crashes. Press your Z-probe limit switch and observe the change in value from 0 to 1000 in the Duet Web Console _Machine Status_ table in the _Z-Probe_ box. If the value does not change the Z-probe is wired or configured wrong, do not continue to the next step!

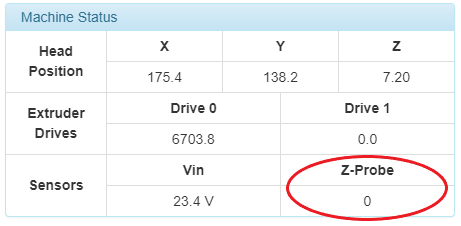
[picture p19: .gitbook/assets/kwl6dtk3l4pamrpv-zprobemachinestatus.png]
   

9. Move the bed towards the nozzle by sending the command `G1 Z20`. When you send the command `G30` the bed will move slowly and precisely to the Z-probe, if you send `G30` while the bed is at `Z100` or greater you will have to wait for a long time for the Z-probe to trigger.
10. Run the command `G30`. This will move the bed toward the z-probe until the limit switch triggers.
11. Now your Z0 is set to your Z-probe limit switches trigger height. This is because the Z-probe limit switch offset is 0mm. Now that we have set our Z0 to the trigger height we can move the bed toward the nozzle in order to find the distance between the trigger height of the Z-probe and the nozzle!
12. Retract the Z-probe.
13. Jog the bed up slowly toward the nozzle using the negative Z buttons in _Machine Control_ on the Duet Web Console. Read the next step!

    

14. As you are moving the bed up towards the nozzle you will encounter an axis limit. These axes limits are set for the X, Y and Z axes and will stop you from moving past a certain coordinate. This will make it harder to crash the printer. However, in this case we know what we are doing so we can disable the axes limits. Send the command `M564 S0` to disable the axis limits. To learn more about this command visit the [RepRap G-code wiki](https://reprap.org/wiki/G-code#M564:_Limit_axes).
15. **Be careful when moving the bed close to the nozzle. Use the 1mm and 0.1mm buttons.** Determining when the bed is touching the nozzle can be difficult. You might have to heat up the nozzle as you learned before in order to ensure that none of the filament from the hot-end gets in the way. Using a piece of paper to determine when the nozzle is touching the bed is also helpful. Grab a sticky-note or small piece of paper and place it under the nozzle. Then carefully jog the bed into the nozzle, move the paper back and forth. When you feel the nozzle grab the paper your nozzle is touching the bed!. 
16. Record the Z-value that the printer is currently displaying in _Machine Status_. The absolute \(non-negative\) of this value is your Z-probe offset. It might be a good idea to write down this value.
17. Enter the command `G31 P999 X-40 Y28.5 Znnn` where `nnn` is your Z-probe offset.
18. Move the bed away from the nozzle `G1 Z20`.
19. Deploy your Z-probe!
20. Send the command `G30`.
21. Move the bed back up to the nozzle as described in the steps above. Your Z value should be 0 when the bed is touching the nozzle. If it is not you might need to tune the Z-probe offset or repeat the process.
22. In order for these changes to take effect permenantly, you will have to open up your _config.g_ file and update the Z-offset of this command there. Follow the section below.

**Your Z-probe offset will not change unless you make changes that can affect the distance between your Z-probe trigger height and your nozzle.**

**Setting the Limit Switch Offset in the Config.g**

### Mechanically Leveling the Bed

Now, we will make sure that the bed is visibly level. Then, we will heat up the bed and perform auto-bed leveling compensation.

1. If your motors are powered, you will not be able to move your bed by hand without skipping the motors. Whenever you activate or power your stepper motors, their position will be held with an idle current. This current will create a permanent stall torque on the motor. In order to disable the idle current on motors you can send the command `M84`. **If your bed is high up, disabling the Z-motor will make the bed drop down.**
2. Lift your bed up from the two points shown in the image below. Lift your bed up to the nozzle.

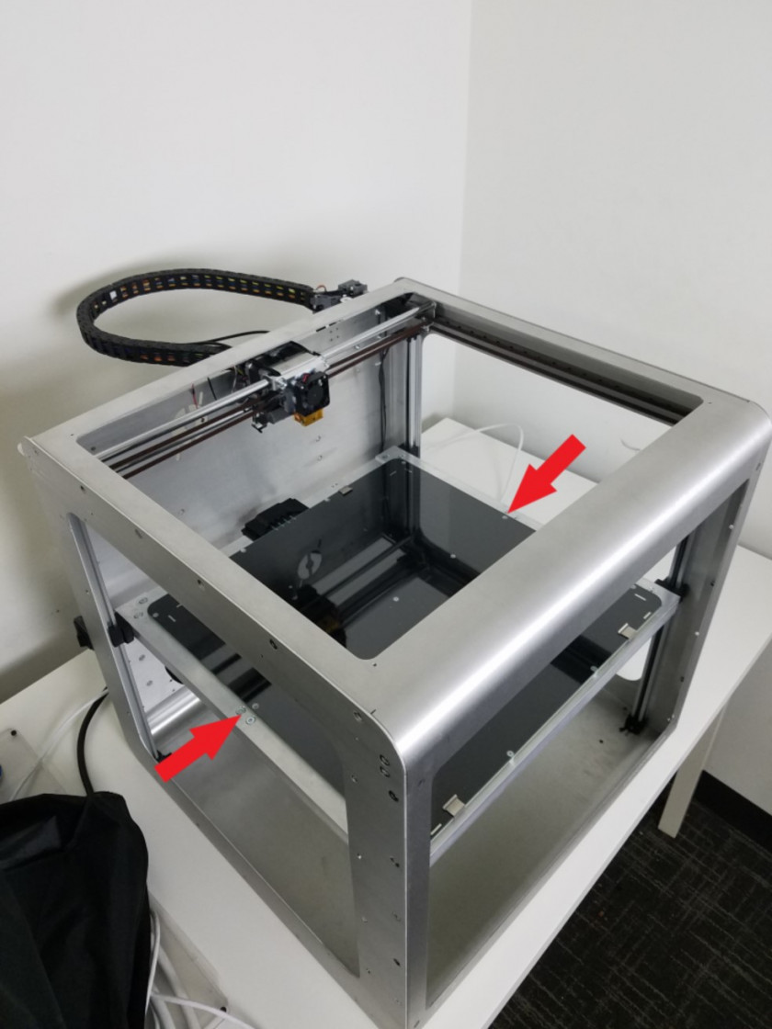
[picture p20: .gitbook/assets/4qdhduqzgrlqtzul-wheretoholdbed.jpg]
   

3. When the bed is touching the nozzle, determine the offset of the Z-sliders to the top belt clamps, as shown in the image below, to determine whether the bed is level. This will give you a good enough estimate to level the bed, bed leveling compensation with `G29` can take care of the rest. The bed can be leveled more accurately by using a caliper to measure the distance between the bed and the top of the Z-slider rails and comparing the corners.

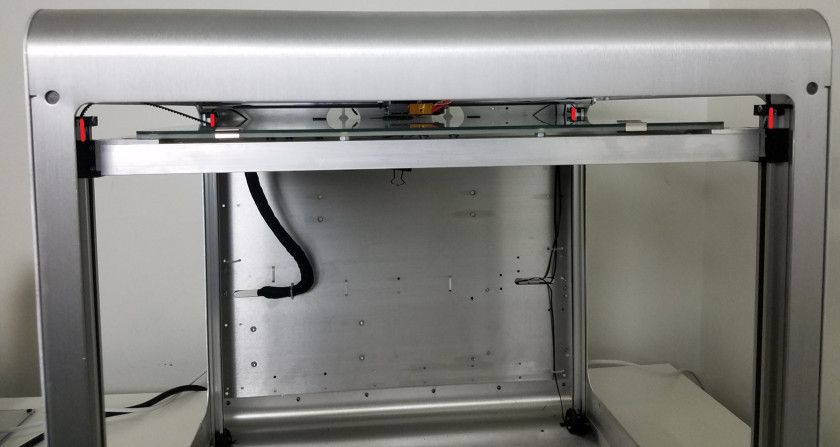
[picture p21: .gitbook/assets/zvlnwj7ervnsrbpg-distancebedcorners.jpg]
   

4. Once you have determined which corner needs to be skipped, lift up the bed about half-way and grab that corner of the bed. Then, gently lift up from that corner until you hear a click and feel the corner give, you have just skipped a belt tooth. Keep repeating this process until all corners of the bed are level. Keep lifting the bed up to the nozzle to check if the bed is level.

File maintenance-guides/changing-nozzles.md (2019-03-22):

# Changing Nozzles

this guide has been updated: please see this video https://youtu.be/qIrvyc5NEUs as the content below is outdated.
Follow the steps below in order to mount a new nozzle on your 3D printer.

{% hint style="warning" %}
**Follow the steps listed in the guide closely. You will be working with heated hot-ends. Use appropriate tools.**
{% endhint %}

Some of the following steps have to be performed with a heated hot-end in order to allow you to slide out and replace the nozzle. If you don't heat your nozzle cooled filament will act like glue and hold the components together. If you have an exceptionally clean or new nozzle then heating is not required

1. Connect to the Duet Web Console.
2. Heat-up the nozzle and retract any filament inside.
3. **Keep the nozzle hot for the next steps!** 
4. Remove the front fan from the QuadFusion by unscrewing the circled screws

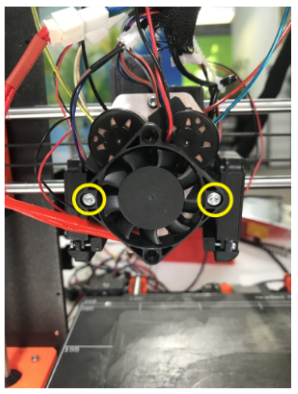
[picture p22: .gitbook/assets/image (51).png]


1. Next, **loosen** the circled screws. Some QuadFusions may not be mounted the same way. Go to [Mounting the Hardware](changing-nozzles.md) for more in depth mount information on certain printers.

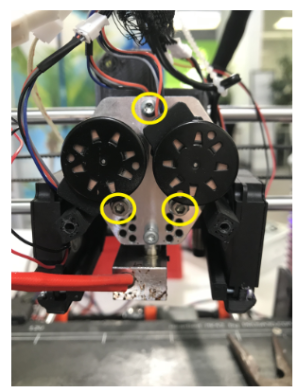
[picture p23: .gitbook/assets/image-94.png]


1. Remove the set-screw holding the nozzle and heater block in place. Carefully retract them using pliers.

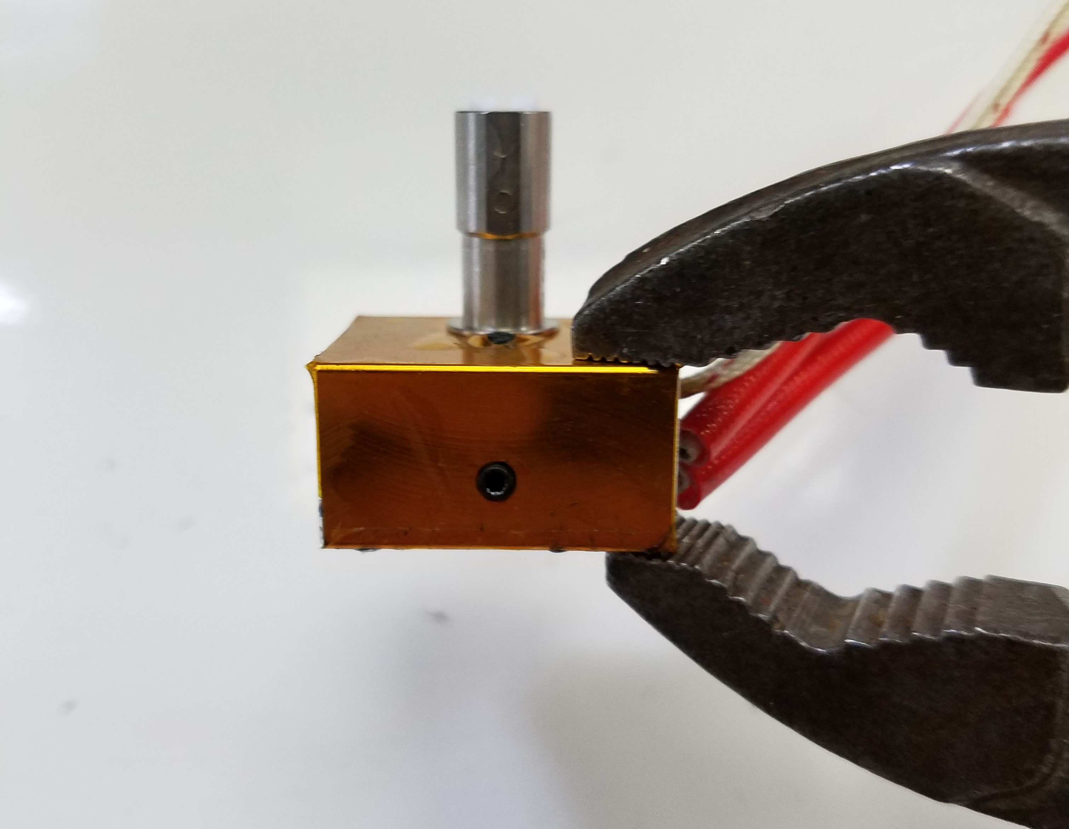
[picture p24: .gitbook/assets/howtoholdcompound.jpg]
   

2. Slide the heater block and cold-section out of the extruder with the pliers.
3. Remove the screw indicated in the image below, this holds the nozzle inside the heater block.

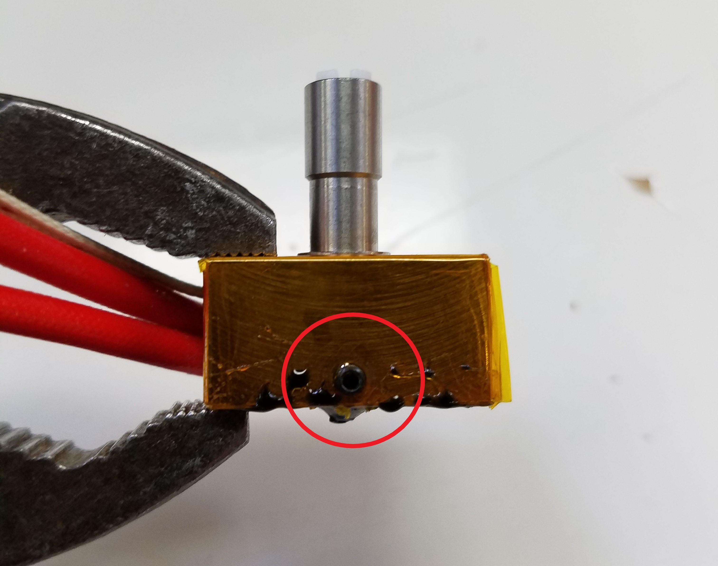
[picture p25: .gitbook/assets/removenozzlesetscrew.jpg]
   

4. With another pair of pliers, carefully pull out the nozzle from the heater block.
5. Place the **hot** nozzle on a heat-resistant surface. If you have a glass bed, you can place the nozzle on there.
6. With the pliers, grab the new nozzle and place it into the heater block, pay attention to the orientation of the nozzle. The dimple should face the set-screw in the heater block. This keeps the heater block in place during operation.

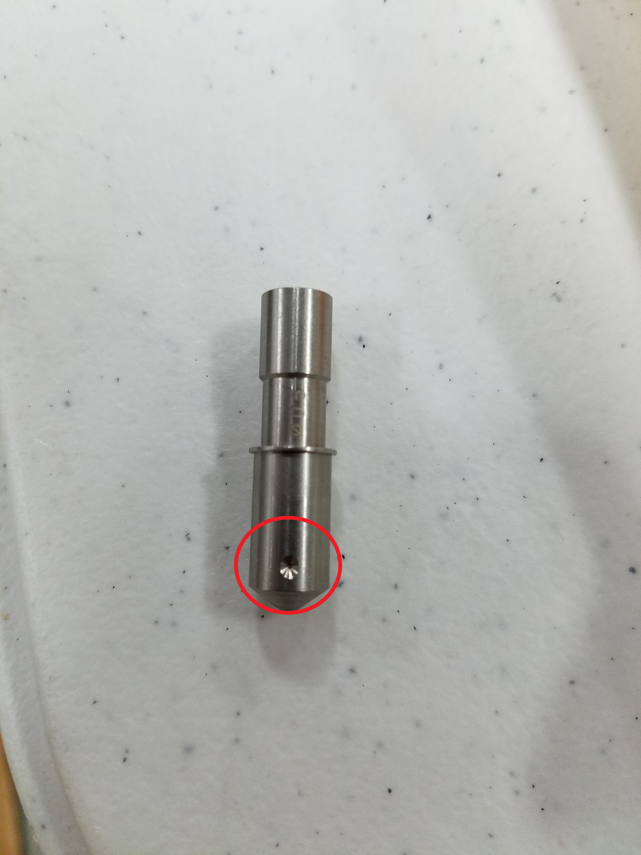
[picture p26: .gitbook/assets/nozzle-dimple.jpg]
   

7. Tighten down the setscrew that holds the nozzle in place.
8. Place the nozzle, with the heater block attached, back into the extruder.
9. Tighten down the setscrews and any other screw you were instructed to loosen.
10. **You can now power off the heater.**
11. You can attach the front fan again and continue printing!

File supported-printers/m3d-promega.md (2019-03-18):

# M3D ProMega

Refer to the [Promega Quad Documentation](http://promega.printm3d.com/quad/repair-and-maintenance/quad-add-on).

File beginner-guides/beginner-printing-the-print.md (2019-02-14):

---
description: A beginner guide about preparing a print on the Crane.
---

# Beginner: Printing the Print

This is the final guide in the Beginner Guides chapter. It will cover how to upload and monitor a print on the Duet Web Console. This guide assumes you have properly configured your printer with all the previous beginner guides. That means:

* You have homed your printer
* You have run and enabled mesh bed leveling
* You have loaded filament into the extruder

## Heating your QuadFusion print head for the first time:

It's important to heat your QuadFusion print head to 235C and allow it to sit for several minuets BEFORE your first print. This will allow you to not only determine if the print head has been connected properly, but it will also allow it to prime for it's first use. 

To do this simply set the temperature to 235C for Tool 0 in the upper left area of your Duet Web Control console.  

Since this is the VERY first time the QuadFusion head has been heated, it may emit an odor. This odor should be slight and it should dissipate within a few minutes. Please make sure your work area is well ventilated during the first heating of your QuadFusion print head.  

## Uploading the G-code File

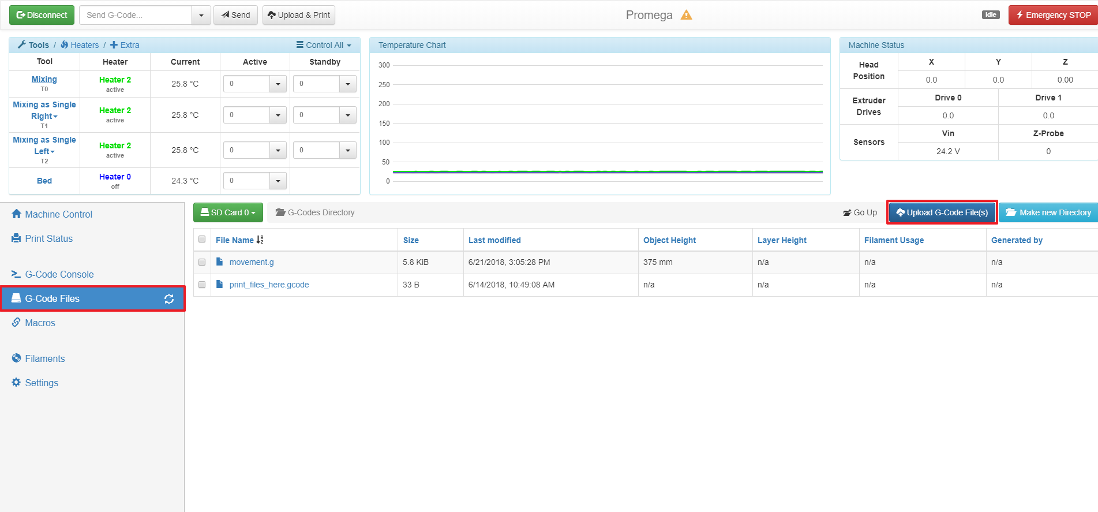
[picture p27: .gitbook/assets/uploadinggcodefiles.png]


First, we will have to upload the G-code file we produced in the previous guide. Connect to the Duet Web Console on the printer. Then, press the _G-code Files_ button and then press the _Upload G-code File\(s\)_ button as shown in the image above. This will open a window which will allow you to select the G-code file you sliced. _Open_ the file and wait for it to upload.

## Printing the File

Once the file is uploaded, you can click the file in order to print it. A window will pop-up confirming that you are about to print something. Click _Yes._

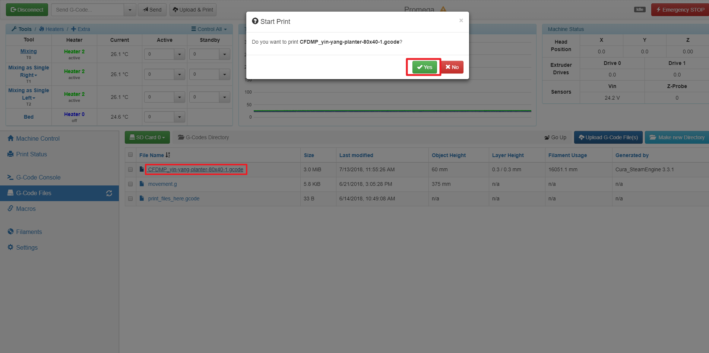
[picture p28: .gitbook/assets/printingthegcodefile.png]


## Monitoring the Print

Now, the print has started. First, the printer will reach it's designated printing temperature that you set in Cura. This might take a while and the printer will not start printing until all components have reached temperature. When the print starts the Duet Web Console will shift over to the _Print Status_ tab on the Duet Web Console. This tab allows you to monitor certain settings of the print. Two of the functions on this tab are very useful: _Z Baby Stepping_ and _Speed Factor_ , these allow you to change the height of the Z and speed while printing. If you notice that a layer is not sticking, try to reduce the speed.

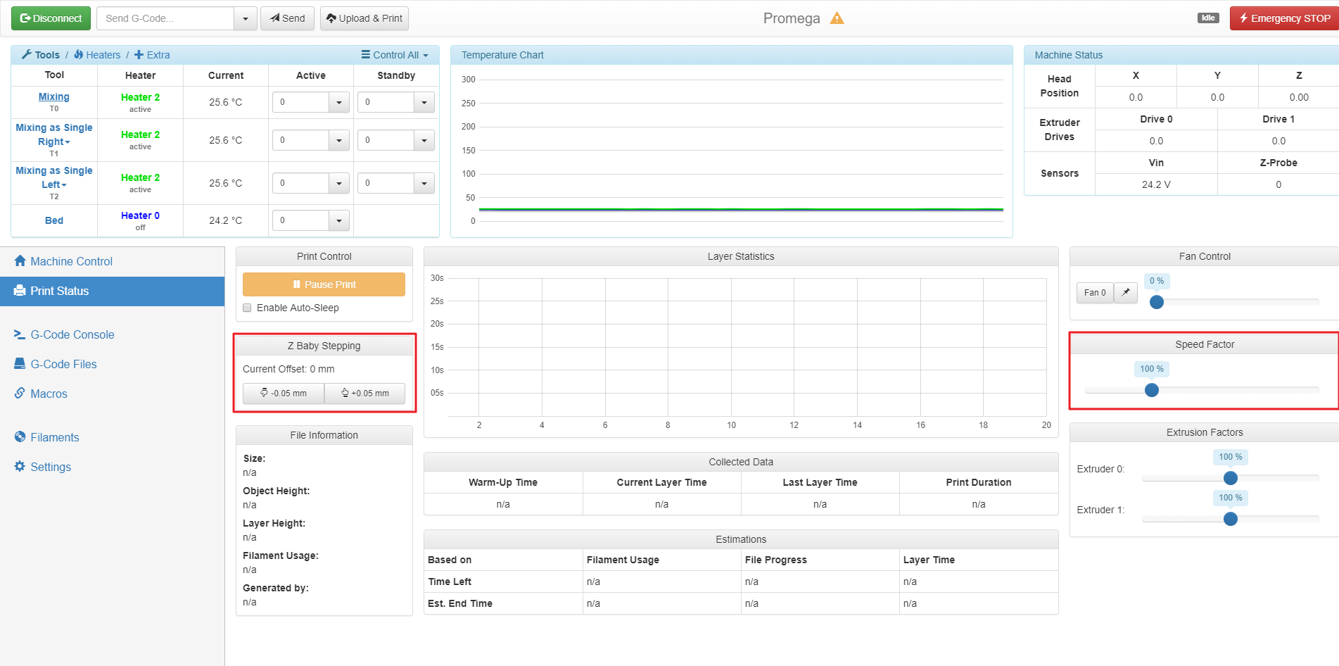
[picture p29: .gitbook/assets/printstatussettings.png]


Your print should now be able to run to completion.

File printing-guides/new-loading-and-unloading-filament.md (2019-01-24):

# \(NEW\) Loading and Unloading Filament

{% hint style="danger" %}
## Warning before loading:

* [ ] Verify that wiring between the Duet 2 Maestro and the M3D Crane \(including wiring to the QuadFusion and other printer components\) is correct.  
* [ ] Verify that the Duet 2 Maestro firmware is updated to the most recent version. You can find version 2.O2 release candidate [here](https://github.com/dc42/RepRapFirmware/releases/download/2.02RC2/DuetMaestroFirmware.bin).  
* [ ] In addition you can find the latest version of Duet Web Control [here](https://github.com/dc42/RepRapFirmware/releases/download/2.02RC2/DuetWebControl-1.22.3.zip). 
* [ ] Be sure to double check that the cold section fan 1 is running at full power. \(This is needed for long term heatbreak cooling\) ****
{% endhint %}

## Filament Reference Table

| Filament type | Temp/Amp |
| :--- | :--- |
| PETG | 170C/400mA |
| PLA |  |

{% hint style="warning" %}
**Be sure to set the temperature to 170C** **Not doing this will cause backflow up the nozzles chambers that will block future loadings!**
{% endhint %}

## Pre-loading Process

* Start by cutting your filament flush. You should start with 4 new strands. **\(poorly cut filament may damage PTFE or bind up in the curved path\)**
* Observe port labeling 0-3 and select extruder drive 0 \(If unlabeled, they are in left to right order and the left most will be extruder drive 0\) 
* Select a feed rate of 5 mm/s \(any faster and it may shred the filament or cause the motor to skip\) 
* Select a 20 mm filament feed amount 

## **Loading Sequence**

1. Insert your chosen filament in to Port 0 and hold it at a curved angle. \(Use the natural curve of the filament to match the curves shown below to minimize any risk of missing the curve path\)  

                                           

2. Press retract while pushing filament lightly in, this is to verify that things are working and that you're in the right position and chose the right port. If the filament is ticking in your hands, go ahead and press the filament towards the gear while pushing the extrude button. \(You should to feel the filament grab and pull through.\) 
3. Lightly hold the filament in your hands and press extrude again until filament stops extruding. Repeat once mote times for a total of 60 mm fed through. 
4. If at any point filament gets stuck proceed to troubleshooting \(Retract and try again. TBD\) 
5. Repeat the above procedure for extruder drive 2 and THEN with ports 1 and 3. 

## Extrusion:

* Set the temp to 240C \(nozzle may ooze ignore it\)
* Change settings to extrude all at 15mm/s and leave the extrude amount at 20mm.
* Confirm your temperature is still set to 240C.
* Hit extrude \(Waiting between steps\) until filament comes out at a steady speed.
* Be sure that no motors are skipping \(if they are see our troubleshooting section TBD\)   ****

## Turning Off your machine:

There are no special considerations for turning off your QuadFusion. However, keep in mind that filament should not be above temperature without motion for longer than 5 minutes, with the exception of PETG; which can handle being held at temperature in the QuadFusion for at least one day.  PLA readily degrades.  

## Unloading:

* Set Nozzle Temperature to 170C.
* Change setting to Extrude All, Extrude at 15mm/s and set the extrusion amount at 100mm
* Press retract 3 times
* The machine may now be turned off

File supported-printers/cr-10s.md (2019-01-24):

# CR-10S

This guide will go through the process of hooking up your QuadFusion to Creality's CR-10S printer.

{% hint style="warning" %}
There is no affiliation between M3D/The QuadFusion and Creality 3D/The CR-10.
{% endhint %}

## Mechanically

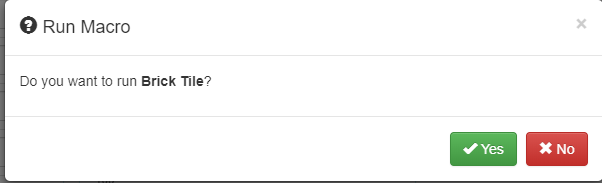
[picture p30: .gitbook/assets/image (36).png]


**You will need...  
-** 3.0mm Standoff \(25mm long\) \(x2\)  
**-** 2.0mm Hex Screws \(x2\)

**Tools  
-** Pliers  
**-** 3.0mm Hex Screwdriver  
**-** 2.0mm Hex Screwdriver

Once you have removed the extruder that comes with the CR-10S, you will want to take of the mounting plate and drill holes using these specs:

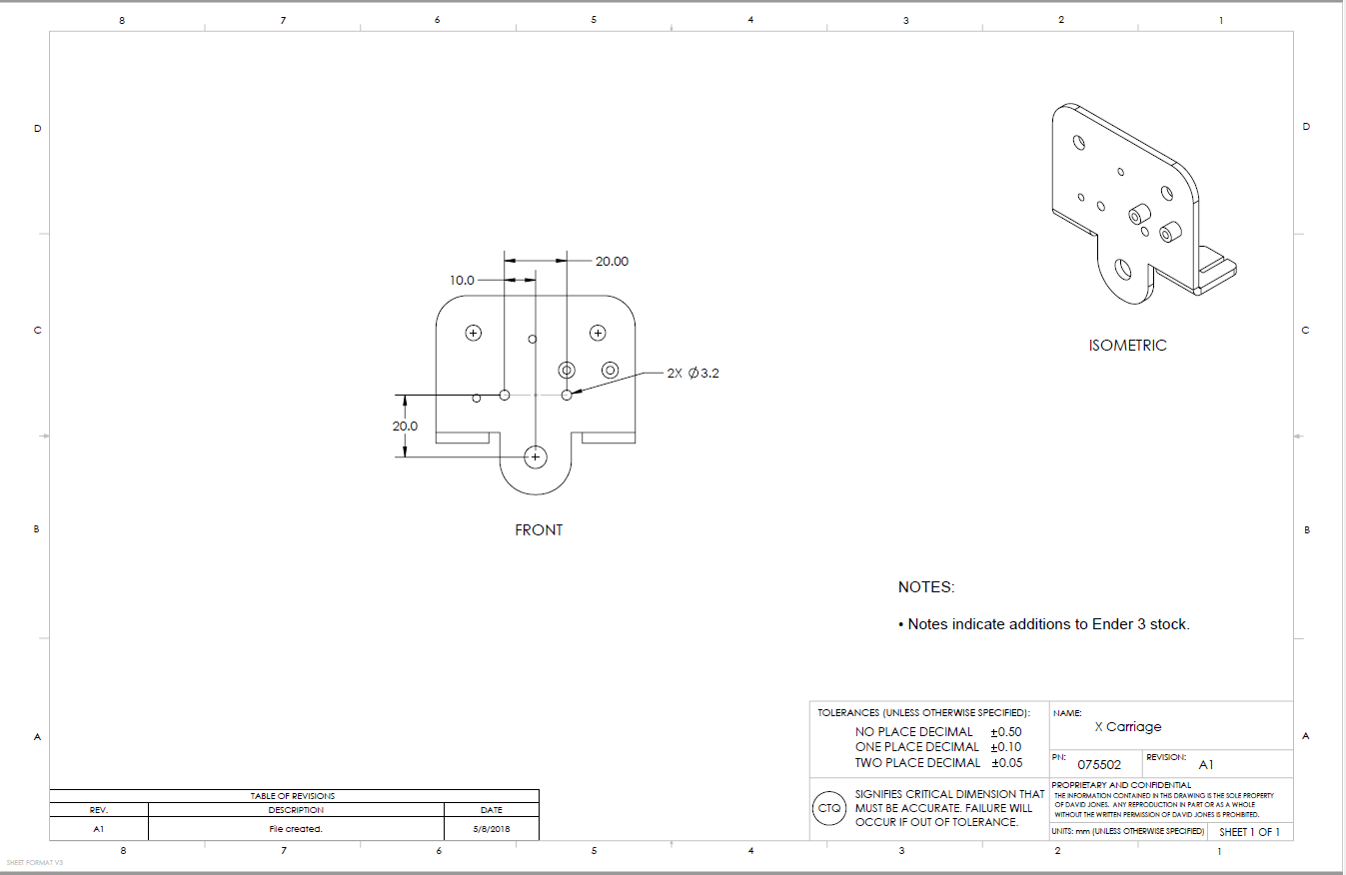
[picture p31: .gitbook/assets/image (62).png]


Alternatively you can print and use this stencil to ensure the drill holes are correctly aligned:

{% file src="../.gitbook/assets/cr10s\_quad\_stencil.stl" caption="CR-10 Quad Stencil" %}

Place the newly drilled plate back on to your CR-10S, attach the top two wheels if you removed them.

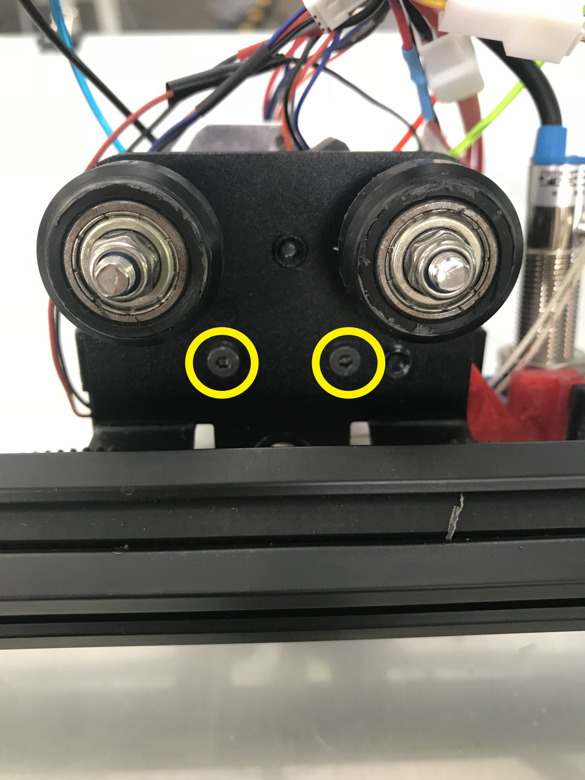
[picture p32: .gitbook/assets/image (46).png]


Next, thread the two 2.0mm Hex Screws through the holes you have just drilled.

Once you have done this, you will want to attach the two 25mm long standoffs to the QuadFusion head.

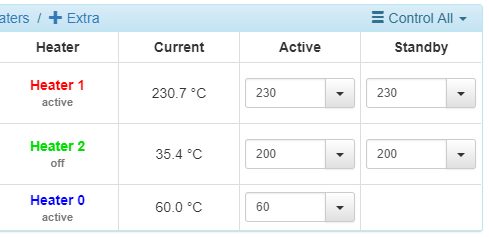
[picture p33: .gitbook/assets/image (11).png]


You can now, by threading the 2.0mm Hex Screws into the standoffs, mount the QuadFusion head onto the CR-10S.

Lastly, attach the bottom wheel:

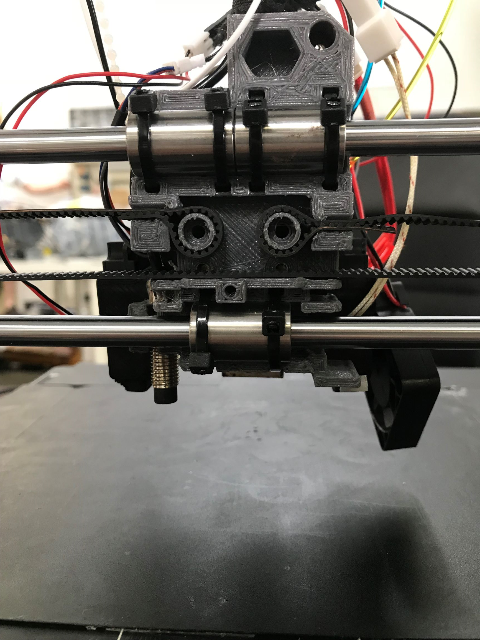
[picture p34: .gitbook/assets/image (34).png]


You have now fully attached the QuadFusion to your CR-10S.

## Electrically

{% hint style="info" %}
You will need a Duet Maestro board if you wish to follow along during the electrical part of this guide. Look at the bottom of the page to see where to get one.
{% endhint %}

{% hint style="info" %}
Go to this link: [https://www.thingiverse.com/search?q=Duet&dwh=345c37c6245e907](https://www.thingiverse.com/search?q=Duet&dwh=345c37c6245e907) if you want to print a Duet Holder. These can be very helpful with protecting and organizing your Duet Maestro!
{% endhint %}

**You will need...  
-** 24V Power Supply  
**-** Duet Maestro Board  
**-** Duet Maestro Expansion Board  
**-** Jumper

**Tools  
-** Flat-Head Screwdriver

This is the Duet Maestro:

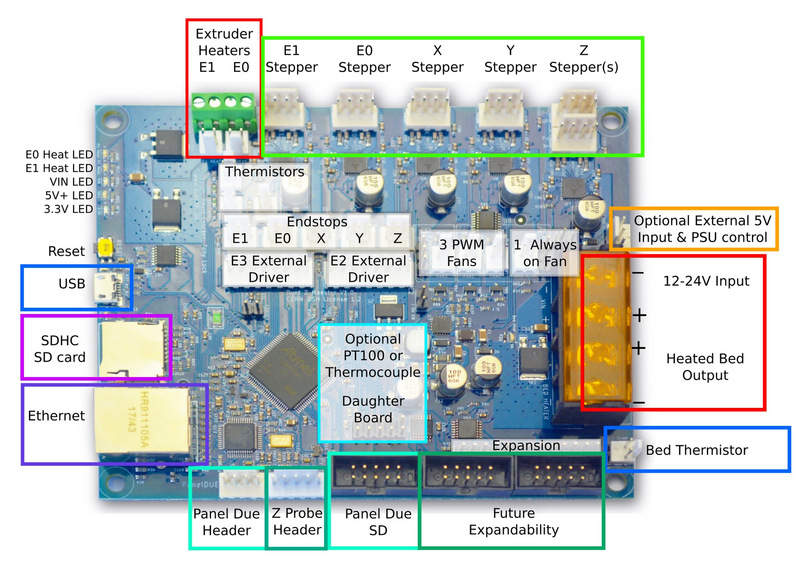
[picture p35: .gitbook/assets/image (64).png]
https://duet3d.dozuki.com/Wiki/Duet\_2\_Maestro\_Hardware\_Overview


This will be a walk through on how to connect the QuadFusion & CR-10 to your Duet Maestro Board with the Extruder Expansion board.

Before you can begin to wire your QuadFusion to the Duet Maestro board you must attach an extension to the board. With this extension you will be able to connect the the extra motor wires to the board.

The following pictures show where the extension goes, and how it looks once it has been plugged in:

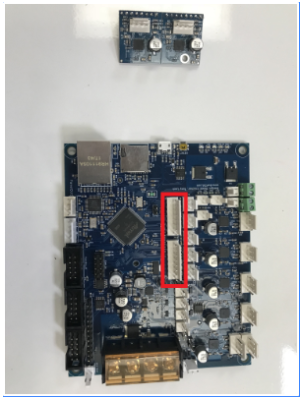
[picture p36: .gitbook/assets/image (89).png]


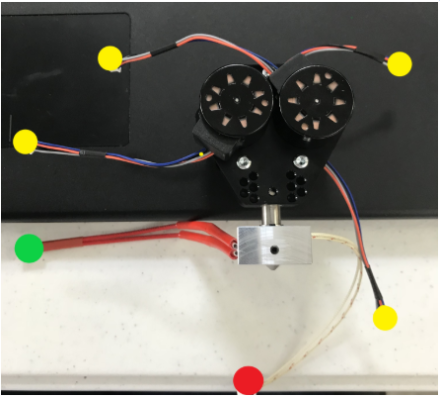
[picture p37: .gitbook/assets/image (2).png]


Additionally, you will need to attach a jumper to the pins next to the expansion board:



### Base Connections



Without the fans, the QuadFusion has six main wires coming from it. The four wires with yellow dots at the ends are the motor wires. The wire with a green dot is the heater wire, and lastly the wire with the red dot is the thermistor.

The wires plug in to their corresponding color that is boxed in the following picture:

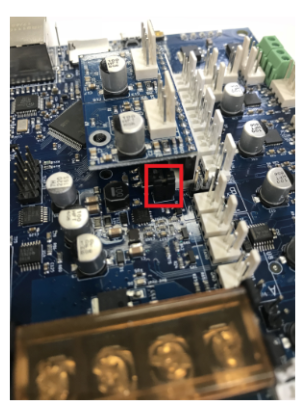
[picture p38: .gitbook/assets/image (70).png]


Notes:

* Keep in mind when you're wiring your QuadFusion's motors to the Duet Maestro board which motor is connected to which port. The first picture in this guide labels each port as E0 Stepper, E1 Stepper, E2 External Driver, and E3 External Driver. When facing the front of your QuadFusion, the front left motor is 0, the front right motor is 2, the back left motor is 1, and the back right motor is 3. 
* If you decide to extend the wires given to you, make sure that you are maintaining the original positive and negative wires. 

The next steps will be to connect your CR-10S' stepper motors, power source, limit switches, and Z-probe

{% hint style="warning" %}
The CR-10S we worked with used a Z-probe instead of the Z-limit switch the printer came with. Additionally, we ended up having the bed heated separately, which will be explained within the guide.
{% endhint %}

Starting with the stepper motors, there are four motors you should be hooking up. One for the X-Stepper motor, one for the Y-Stepper motor, and two for the Z-Stepper motors.



If you look above, the boxed sections are where you will be plugging in your stepper motors. The color coordination is as follows;  
Yellow = X-Stepper Motor  
Orange = Y-Stepper Motor  
Green = Z-Stepper Motors

Once you have plugged these in you can move on to connecting the power supply. **You will need a 24V power supply** to power your Duet Maestro board

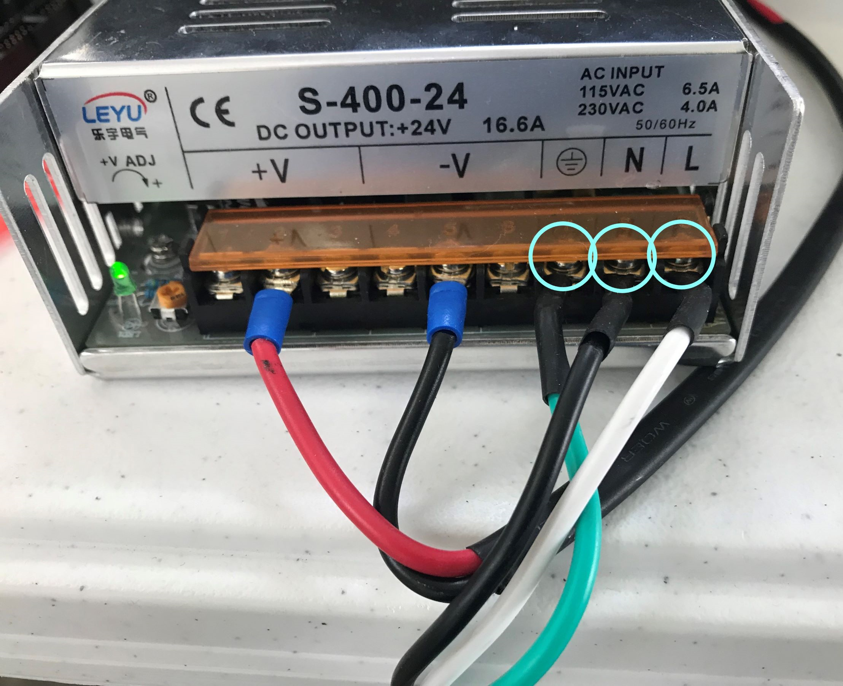
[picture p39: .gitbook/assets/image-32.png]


The three circled wires are what will be connecting your power supply to an outlet. The non circled wires are what will be connected to your Duet Maestro board

{% hint style="info" %}
We recommend having an on/off switch between the power supply and Duet Maestro board, this makes it easier to turn your printer on and off.
{% endhint %}

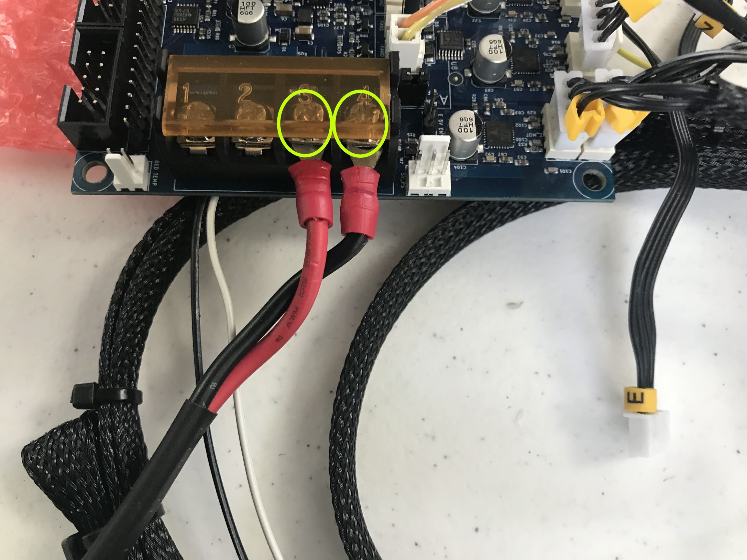
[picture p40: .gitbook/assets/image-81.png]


The red and black wires will be connected to ports 3 and 4, respectively, as shown in the image above.

Lastly, you'll need to connect the Z-probe and limit switches. Starting with the limit switches:



The picture above shows where each limit switch should be connected. Color coordination is as follows;  
Yellow = X-Limit Switch  
Red = Y-Limit Switch  
Aqua = Z-Limit Switch

Now, if you are using a Z-probe as we did, you will be connecting the probe to the Duet Maestro board based off of your probe's specific wiring

Go here to understand how Duet wires Z-probes to their boards:  
Choosing a Z-probe: [https://duet3d.dozuki.com/Wiki/Choosing\_a\_Z\_probe](https://duet3d.dozuki.com/Wiki/Choosing_a_Z_probe)  
Connecting a Z-probe: [https://duet3d.dozuki.com/Wiki/Connecting\_a\_Z\_probe](https://duet3d.dozuki.com/Wiki/Connecting_a_Z_probe)

**Attaching the LCD Screen**

To attach the LCD screen to your Duet Maestro you will need to use these ribbon cables provided in the upgrade kit given to you. You will plug the cables into the Duet Maestro in ports labeled "Future Expandability"



Finally, attach the cables to your LCD screen.

**Heating the Bed**

The bed was wired separately from the main collection of wires because of the power supply. The QuadFusion requires a 24V power supply in order to properly power the motors, heater, and thermistor. However, the bed could only be safely powered by 12V, so it was decided to have the bed remain wired to Creality's original board. Because of this, you will be able to heat your bed from the control block that comes with the printer, as opposed to heating with the Duet Web Control.

Don't have something that is listed here? Check out these links if you need something for the QuadFusion!

24V power supply: [https://store.printm3d.com/collections/parts/products/400w-power-supply?variant=12283391148110](https://store.printm3d.com/collections/parts/products/400w-power-supply?variant=12283391148110)  
Duet Maestro Board: [https://fitforlaunch.com/projects/duet-2-maestro](https://fitforlaunch.com/projects/duet-2-maestro)  
Extruder Expansion Board: [https://store.printm3d.com/products/copy-of-duet-2-maestro-expansion?variant=21198635434062](https://store.printm3d.com/products/copy-of-duet-2-maestro-expansion?variant=21198635434062)  
Toggle Switch: [https://store.printm3d.com/collections/parts/products/lighted-toggle-switch?variant=12283706245198](https://store.printm3d.com/collections/parts/products/lighted-toggle-switch?variant=12283706245198)

Thank you for supporting the QuadFusion, and Happy Printing!

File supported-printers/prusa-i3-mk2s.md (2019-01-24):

# Prusa i3 MK2S

This guide will go through the process of hooking up your QuadFusion to Prusa's i3 MK2S printer.

{% hint style="warning" %}
There is no affiliation between M3D/The QuadFusion and Prusa/The i3 MK2S
{% endhint %}

## Mechanically

The Prusa i3 MK2S requires an entirely new extruder mount in order to mount the QuadFusion. The new mount is very similar to the old, only a few things were shifted around to accommodate the new extruder.

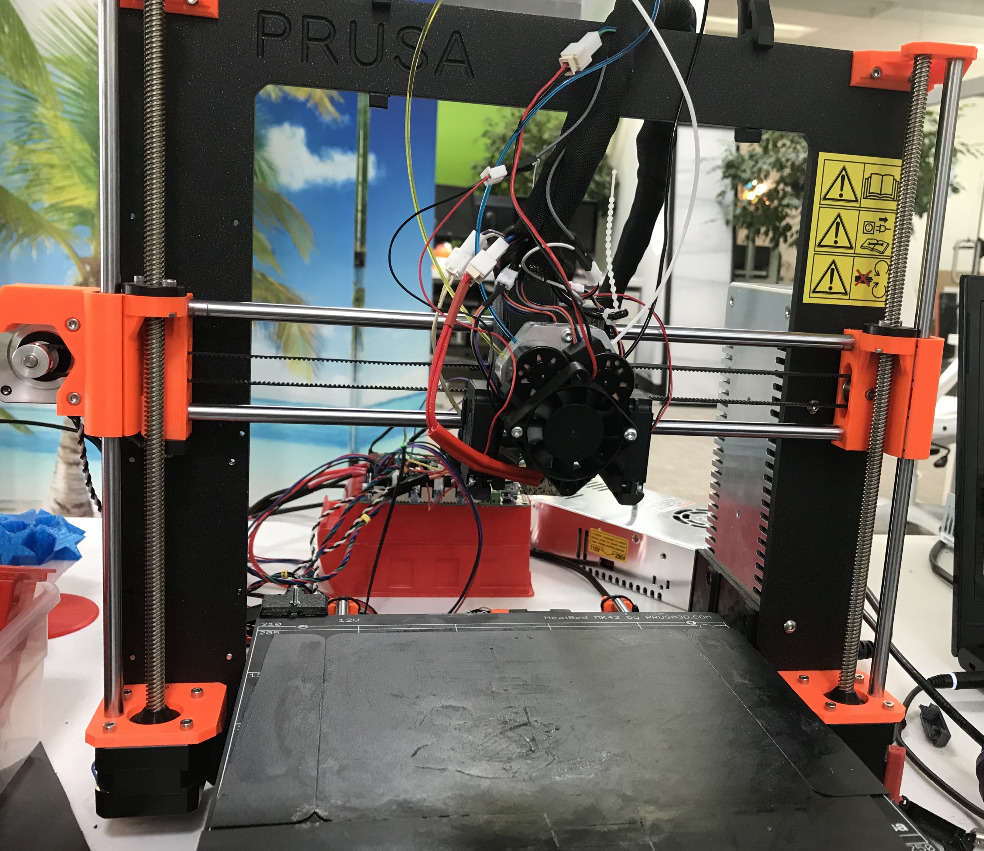
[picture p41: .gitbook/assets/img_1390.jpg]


**You will need...**  
**-** 3mm Hex Standoffs \(20mm long\) \(x2\)  
**-** 3mm Hex Screw \(33mm long\) \(x2\)  
**-** QuadFusion Mount \(Downloadable under "STL File\(s\)"\) **-** Zip-ties \(x6\)

**Tools...**  
**-** 2.5mm Hex Screwdriver

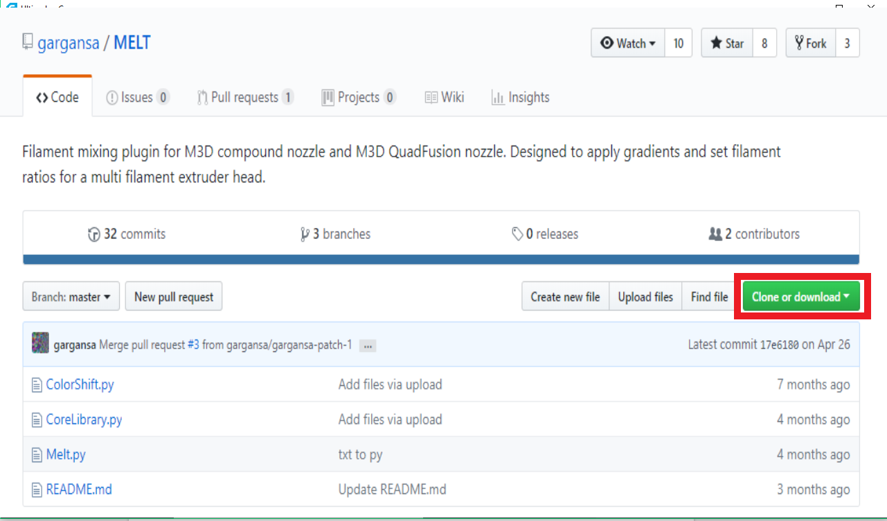
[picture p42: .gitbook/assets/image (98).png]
Front


The front of the mount has 4 holes, screw the two 20mm long standoffs into the 2 lower holes, as shown in the image below

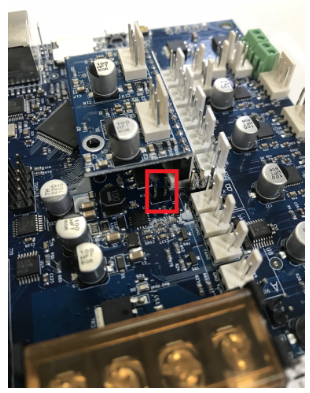
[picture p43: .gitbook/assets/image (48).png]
Back


The back of the mount shows where it will be mounted to the Prusa. The lower X-belt will lie across the ledge of the mount. While the upper X-belt will be wrapped around the two protruding cylinders. You can tighten the X-belt by wrapping more of the belt around the cylinder, as shown in the picture above.  
Additionally, the mount is attached to the Prusa using six zip-ties. Theses zip-ties can be routed through designated holes that the mount contains.

Lastly, using the 33mm long Hex Screws, thread the screw into the QuadFusion till the come out the other end and thread into the standoffs.

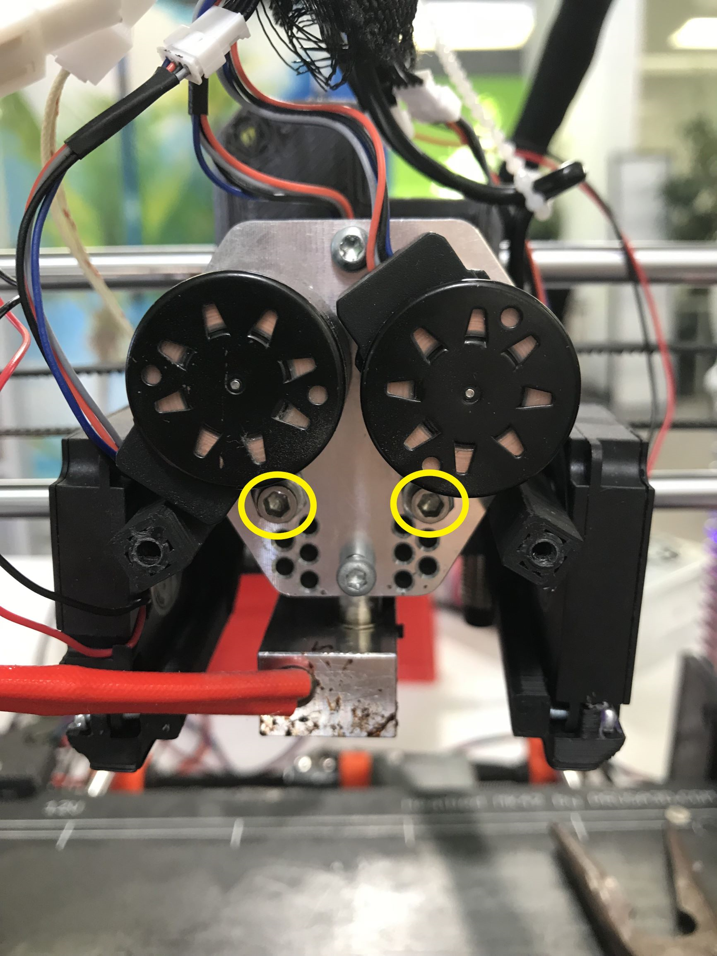
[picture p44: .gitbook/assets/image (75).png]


You have now fully attached the QuadFusion to your i3 MK2S.

**STL File\(s\):**

{% file src="../.gitbook/assets/prusa\_quad\_mount.STL" caption="Prusa\_Quad\_Mount" %}

## **Electrically**

{% hint style="info" %}
You will need a Duet Maestro board if you wish to follow along during the electrical part of this guide. Look at the bottom of the page to see where to get one.
{% endhint %}

{% hint style="info" %}
Go to this link: [https://www.thingiverse.com/search?q=Duet&dwh=345c37c6245e907](https://www.thingiverse.com/search?q=Duet&dwh=345c37c6245e907) if you want to print a Duet Holder. These can be very helpful with protecting and organizing your Duet Maestro!
{% endhint %}

**You will need...  
-** 24V Power Supply  
**-** Duet Maestro Board  
**-** Duet Maestro Expansion Board  
**-** Jumper  
**-** Terminal board

**Tools  
-** Flat-Head Screwdriver

This is the Duet Maestro:

https://duet3d.dozuki.com/Wiki/Duet\_2\_Maestro\_Hardware\_Overview

This will be a walk through on how to connect the QuadFusion, as well as part of the i3 MK2S, to the Duet Maestro board.

Before you can begin to wire your QuadFusion to the Duet Maestro board you must attach an extension to the board. With this extension you will be able to connect the the extra motor wires to the board.

The following pictures show where the extension goes, and how it looks once it has been plugged in:





Additionally, you will need to attach a jumper to the pins next to the expansion board:



### Base Connections



Without the fans, the QuadFusion has six main wires coming from it. The four wires with yellow dots at the ends are the motor wires. The wire with a green dot is the heater wire, and lastly the wire with the red dot is the thermistor.

The wires plug in to their corresponding color that is boxed in the following picture:



Notes:

* Keep in mind when you're wiring your QuadFusion's motors to the Duet Maestro board which motor is connected to which port. The first picture in this guide labels each port as E0 Stepper, E1 Stepper, E2 External Driver, and E3 External Driver. When facing the front of your QuadFusion, the front left motor is 0, the front right motor is 2, the back left motor is 1, and the back right motor is 3. 
* If you decide to extend the wires given to you, make sure that you are maintaining the original positive and negative wires. 

The next steps will be to connect your i3 MK2S' stepper motors, power source, limit switches and Z-probe.

{% hint style="info" %}
The bed is not connected to the Duet Maestro board, this will be further explained in this guide.
{% endhint %}

Starting with the stepper motors, each one will plug into one of these highlighted ports:



The color coordination is as follows;  
Yellow = X-Stepper Motor  
Orange = Y-Stepper Motor  
Green = Z-Stepper Motors

{% hint style="warning" %}
The original connectors on the i3 MK2S' electrical board are not compatible with the Duet Maestro. We recommend cutting off the locking mechanisms on each connector since they interfer with plugging the wires into the Duet Maestro.
{% endhint %}

The next step is to wire the limit switches and Z-probe to these highlighted ports:



The picture above shows where each limit switch and the Z-probe should be connected. Color coordination is as follows;  
Yellow = X-Limit Switch  
Red = Y-Limit Switch  
Green = Z-Probe

When attaching the Z-probe you will need to use some Dupont connectors in order to properly connect it to the Duet Maestro:

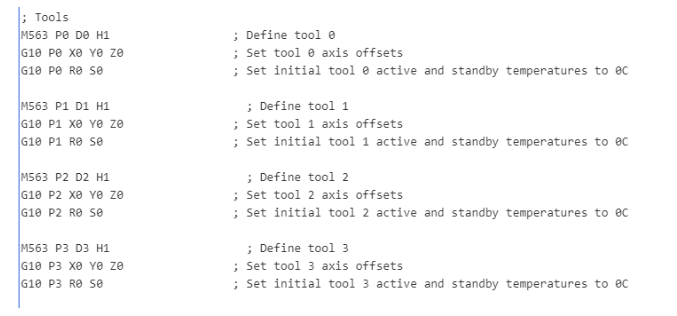
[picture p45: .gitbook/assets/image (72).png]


Color coordination is as follows:  
The black wire represents the Z-probe's black wire  
The grey wire represents the Z-probe's blue wire  
The brown wire represents the Z-probe's brown wire

After plugging these in you can move on to connecting the power supply. **You will need a 24V power supply** to power your Duet Maestro board



The three circled wires are what will be connecting your power supply to an outlet. The non circled wires are what will be connecting to your Duet Maestro board

{% hint style="info" %}
We recommend having an on/off switch between the power supply and Duet Maestro board, this makes it easier to turn your printer on and off.
{% endhint %}



The red and black wires will be connecting to ports 3 and 4, respectively, as shown in the image above.

**Attaching the LCD Screen**

To attach the LCD screen to your Duet Maestro you will need to use these ribbon cables provided in the upgrade kit given to you. You will plug the cables into the Duet Maestro in ports labeled "Future Expandability"



Finally, attach the cables to your LCD screen.

**Heating the Bed**

The bed was wired separately from the main collection of wires because of the power supply. The QuadFusion requires a 24V power supply in order to properly power the motors, heater, and thermistor. However, the bed could only be safely powered by 12V, so it was decided to have the bed remain wired to Prusa's original power source, but also be connected to the Duest Maestro.

{% hint style="warning" %}
Make sure you make the same connections, in the same location, that are described and pictured below.
{% endhint %}

To begin, the bed's heater wire will be attaching to the Duet Maestro here:





Once you have done this you will want to use a terminal board to make further connections. Take the two wires coming from the back of your Prusa i3 MK2S and connect them on the same side, like so:



Color coordination:  
The yellow circled wire is the plain black wire.  
The green circled wire is the black wire with a red stripe.

Next, you will want to create you own wire, preferably with a loop connector, that connects from the terminal board to the Duet Maestro's positive Port 1. As shown below:





The following step is to make a another wire connecting a 24V power supply's negative port to the terminal board:





The last connections to make are those from the 12V power supply, that Prusa has with the i3 MK2S, to the terminal board:



Color coordination:  
The blue circled wire will be black and have a red stripe on it.  
The yellow circled wire will be plain black.

Don't have something that is listed here? Check out these links if you need something for the QuadFusion!

24V power supply: [https://store.printm3d.com/collections/parts/products/400w-power-supply?variant=12283391148110](https://store.printm3d.com/collections/parts/products/400w-power-supply?variant=12283391148110)  
Duet Maestro Board: [https://fitforlaunch.com/projects/duet-2-maestro](https://fitforlaunch.com/projects/duet-2-maestro)  
Extruder Expansion Board: [https://store.printm3d.com/products/copy-of-duet-2-maestro-expansion?variant=21198635434062](https://store.printm3d.com/products/copy-of-duet-2-maestro-expansion?variant=21198635434062)  
Toggle Switch: [https://store.printm3d.com/collections/parts/products/lighted-toggle-switch?variant=12283706245198](https://store.printm3d.com/collections/parts/products/lighted-toggle-switch?variant=12283706245198)

Thank you for supporting the QuadFusion, and Happy Printing!

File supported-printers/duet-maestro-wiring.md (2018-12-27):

---
description: Learn more about the wiring of the Crane printer on the Duet Maestro side.
---

# Duet Maestro Wiring

This guide covers the wiring of the Crane along with possible wiring solutions to problems. Properly understanding the wiring of the Crane is extremely important. Shorting the Duet Maestro board can be done easily. Follow and acknowledge the warnings listed in [Critical Warnings](https://m3d.gitbook.io/promega-docs/getting-started/critical-warnings-and-information). The Duet Maestro board can be easily damaged or broken by:

1. Wiring the board incorrectly and causing a short
2. Electro-static Discharge
3. Generating too much voltage by manually moving motors
4. Plugging in and unplugging components while the system is powered
5. Touching electrical components while the system is powered

## Wiring Guide

### Duet Maestro Ports

Duet Maestro Component Diagram

The image above displays the ports found on the Duet Maestro and their functions.

Before you can begin to wire your QuadFusion to the Duet Maestro board you must attach an extension to the board. With this extension you will be able to connect the the extra motor wires to the board.

The following pictures show where the extension goes, and how it looks once it has been plugged in:





### Base Connections



Without the fans, the QuadFusion has six main wires coming from it. The four wires with yellow dots at the ends are the motor wires. The wire with a green dot is the heater wire, and lastly the wire with the red dot is the PT1000 \(or thermistor\).

The wires plug in to their corresponding color that is boxed in the following picture:



Notes:

* Keep in mind when you're wiring your QuadFusion's motors to the Duet Maestro board which motor is connected to which port. The first picture in this guide labels each port as E0 Stepper, E1 Stepper, E2 External Driver, and E3 External Driver. When facing the front of your QuadFusion, the front left motor is 0, the front right motor is 2, the back left motor is 1, and the back right motor is 3. 
* If you decide to extend the wires given to you, make sure that you are maintaining the original positive and negative wires. 

**Connecting the fans**

{% hint style="info" %}
Make sure to have your hotend fans connected to the 5V port. Look at the Jumpers section to see how to do so.
{% endhint %}

There are three fans connected to the QuadFusion, two small fans on the left and right and one large fan on the front. The large fan on the front is Fan 0, or "Always On", the two side fans are connected to one another and make up Fan 1 \(whose speed can be controlled in the Duet Web Control\).

In the picture below, the red box indicates where Fan 0 should be plugged in, and the blue box is where Fan 1 is to be plugged in.



### Crane Resistance Table

The Crane electrical components have specific resistances attributed to them. This can make troubleshooting components much easier. With a multi-meter set to measure resistance, you can measure the resistance of a thermistor or heater and compare the reading with the values in the table below. Whenever you are working with electrical components we recommend you switch off the power to the Duet board!

**Resistance Table**

| Component | Expected Value \(Ω\) |
| :--- | :--- |
| Extruder PT1000 | 1090\* Ω |
| Extruder Heater | 13.1 Ω |
| Bed | 2.2 Ω |
| Bed Thermistor | 106800\* Ω |
| Extruder Stepper Motor | 19.3 Ω |
| Axis Stepper Motor | 9.0 Ω |

\*Remember that the resistance of a thermistor is dependent on temperature and will vary from this reading! Thermistor resistance values listed above were taken at room temperature \(~24 C\)

### Jumpers

You might notice that your Duet Maestro board for the Crane came with several jumpers on the board. In case you are not familiar with what a jumper is, it represents a connector bridging two electrical components or signals. Read this for more about jumpers: \[Wikipedia: Jumpers\]\([https://en.wikipedia.org/wiki/Jumper\_\(computing](https://en.wikipedia.org/wiki/Jumper_%28computing)\)\). Your Duet should have 5 different jumpers, located as seen in the image below.

Duet Maestro Jumper Placement

Jumpers:

1. Allows for internal 5V power when Vin \(24V\) is connected
2. Fan voltage jumper, B FAN2, set to 5V for nozzle fan
3. Fan voltage jumper, A Always-on-fan set to Vin for cold-section fan
4. and 5. Only one Z-motor on the Crane, so jumpers are required to properly connect Z-motor to the stepper motor driver.

{% hint style="info" %}
You will need Jumper \#1 in order to connect the third and fourth motor from the QuadFusion to the Duet Maestro
{% endhint %}

The pictures below depict where the jumper needs to go, and how it looks once it is there:





### Before you continue

If you change the wiring of your printer it is best to proceed with the following steps before continuing to prevent damage.

1. Double check the wiring of every single wire you changed. 
2. Plug in the power supply while the printer is switched **off**. 
3. Turn the printer on 
4. Connect to the Duet Web Console 
5. Verify the temperature readouts of all heating components. 
6. Test each component individually
   1. Move each motor independently and confirm that it is travelling in the correct direction.
   2. Heat up your nozzle\(s\)
   3. Heat up your bed
   4. Press each limit switch
7. You should be ready to go!

### Extra Resources:

There is way more to the electronics of the Duet Maestro board. Follow the links below for more help and information regarding the Duet Maestro.

1. [Duet Maestro Pinout](https://duet3d.dozuki.com/Wiki/Duet_2_Maestro_Wiring_Diagram) 
2. [Duet Maestro Hardware Overview](https://duet3d.dozuki.com/Wiki/Duet_2_Maestro_Hardware_Overview#Section_Wiring_and_pinout) 
3. [M3D Support](https://printm3d.com/support) 
4. [Duet3D forum](https://forum.duet3d.com/): A great place for very specific Duet Maestro and RepRap firmware questions

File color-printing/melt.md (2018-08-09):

# MELT

This guide will go through step-by-step on how to print a simple gradient design using MELT. This guide will assume you have already downloaded MELT, and have picked your own print file.

To start, open you file up in Cura and selct Extensions --&gt; Post Processing --&gt; Modify G-Code



Next you will want to select the drop down tab "Add a Script" 



Select "Multi-Extruder Layering Tool 3.4.0 \(MELT\)"



Based upon your file you will want to edit your basic settings to fit your print. Below is how the settings were altered for this example print:



**Settings Explained:**  
_Number of Extruders:_  
This setting declares how many filaments you wish to use. With the QuadFusion, you can select up to all four filaments.  
_Shifting Clamp Type:_  
You can decided whether you want to print in gradient based on the layer number of your file, or the percentage of your file.  
_Extrusion \# Start:_  
This instruct the printer to begin the gradient at a certain layer number or a certain percentage of your file.  
_Extrusion \# End:_  
This instruct the printer to end the gradient at a certain layer number or a certain percentage of your file.  
_Shift Frequency:_  
This instructs your printer how fast or slow you want it to take to transition to the next gradient ratio. 

Next, you will want to select "Expert Controls" and "Enable Initial Setup".



**Settings Explained:**  
_Define Tool:_  
This section is a `M563` command designed so the user can specifically select which drive they wish to have used when printing gradient. \(e.g. In the example above, by using Drives 0,1,2, and 3, all four filaments will be extruded in gradient\).  
_Initial Main Flow:_  
This instructs the printer what ratio it should begin the print \(e.g. In the example above, the printer will begin with printing 100% of Drive 0\)  
_Final Main Flow:_  
This instructs the printer what ratio it should end the print \(e.g. In the example above, the printer will end with printing 100% of Drive 3\)

From this point on you can edit your slicer settings however you see fit.

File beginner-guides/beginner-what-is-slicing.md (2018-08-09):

---
description: An explanation for beginners about slicing.
---

# Beginner: What is Slicing?

Whenever you want to print a model you will have to convert the model to a _.gcode_ file type. This file type is a huge list of G-code commands that the Duet Board will process one by one in order to achieve a complete print. The G-code file is generated by software called a slicer. A slicer takes a model applies certain print and printer settings and generates the _.gcode_ file. The model also has to be of a specific file type called a _.STL._ This file type can be generated from a CAD model that you designed or downloaded from the internet from websites such as [Thingiverse](https://www.thingiverse.com/), [Pinshape,](https://pinshape.com/) [MyMiniFactory ](https://www.myminifactory.com/)and many others!

## Finding an _.STL_ File

It is possible to create your own _.STL_ file by downloading a CAD \(Computer Assisted Design\) software such as SolidWorks or [TinkerCAD](https://www.tinkercad.com/). However, in order to take things one step at a time, we will go online and download a working model from the internet. This is because multiple constraints of the 3D printer have to be taken into account when designing a model for printing with a 3D printer.

Go to one of the websites listed above and download a _.STL_ model of something you would want to print. For this guide I am going to use this model: [Customizable Yin-Yang Planter / Container](https://www.thingiverse.com/thing:2531208) by [Lucina M](https://www.thingiverse.com/Lucina/about). Follow the red markings below. Click Thing Files and then click the models you want to download the ._STL_ files of. These files will then end up in your downloads folder.



Next, we will move on to installing a slicer to slice the models we just downloaded.

## Installing Cura

For this guide we will use Cura to slice our model. [Download it here!](https://ultimaker.com/en/products/ultimaker-cura-software)

Continue with the installation process until you are able to launch Cura.

### Configuring Cura

Open Cura's Setting by pressing _Preferences &gt; Configure Cura._



Once you have opened Cura's settings we will go to add a printer. This is because we need to tell Cura the specifics of our printer, such as the maximum build volume of the printer. Press _Printers_ and then _Add_ in order to add a new printer. This will open a new window.



Next, press _Custom._ This indicates we are adding a custom printer to Cura's loadout. You can define the _Printer Name_ however you want. Then press _Add Printer,_ this should open another setting window_._



This window allows you to configure the printer settings of the Crane. This informs Cura of the Crane's build space, the firmware flavor and specifies starting and ending G-code. The build volume of the printer represents the maximum value that the printer can travel in each direction. The firmware flavor is the type of firmware that the board is running. The Duet Maestro board runs on RepRap firmware. Your firmware flavor indicates what type of commands the board can understand. The starting and ending G-code is a series of commands that are run at the start and at the end of every print. This is important as it allows you to retract your filament after the print and turn all the heaters off. Configure the settings in this window exactly as shown in the image below.



`; Starting G-code:    
G28 ;Home    
;Prime the extruder    
G92 E0    
G1 F200 E3    
G92 E0`

`; Ending G-code    
M104 S0    
M140 S0    
;Retract the filament    
G92 E1    
G1 E-1 F300    
G28 X0 Y0    
M84`

**Don't click** _**Close**_ **just yet!** Move on to the _Extruder 1_ tab and fill in the following information. Fill in the nozzle diameter and the material diameter. Your nozzle diameter may vary in the future as you mount different types of nozzles on the Crane. Then you can click _Close._



Once you have added the printer make sure to activate it by selecting the name and then clicking the button _Activate._

### Importing the Printer Profile

The next step is to go to the M3D GitHub Crane repository, in the [Cura Profiles folder](https://github.com/PrintM3D/Crane/tree/devel/Cura%20Profiles) and download the Cura profile for your extruder setup. In order to download the Cura Profile, click on the file in GitHub and then press the Download button as seen in the image below, outline in red. This profile contains all kinds of print settings that help the Crane print well. You can find and tune these settings through experimentation at a later time. For now, this default profile will work well.



In Cura, open the Preferences again by clicking _Preferences &gt; Configure Cura._ Click _Profiles &gt; Import_. Then a window will pop up that will allow you to navigate to the profile you just downloaded. It will most likely be in the _Downloads_ folder.



Once you have properly imported the file you will have to _Activate_ it. Select the profile and click the button _Activate._ The print settings you just downloaded have now been applied to Cura. Whenever you slice a model, it will now incorporate these settings.



## How Cura Works

Now that you have properly configured Cura, we can go over how it operates, and how you can configure it. Look at the diagram below for a simple drawing of the most important functions of Cura. The buttons on the left side allow you to load a model into Cura. This is very important as loading a model into Cura begins the slicing process. The buttons below the _Open File_ button allow you to manipulate the position, orientation and scale of the model. This is very important. On the right of the window you have buttons to select your material, and _Advanced Settings._ This tab allows you to configure the finer details of the print as you print with your Crane. Mastering the settings of this tab is extremely useful in order to produce fine and high detail prints. Before you print you should always review the settings in this tab in order to ensure that the printing temperature and other settings is correct for your print and material. Whenever you configure your settings and have your print in the correct position and orientation, you can click Prepare in the bottom right corner. Cura will then take a few seconds to slice the file and create a _.gcode_ file. You will then be able to click the button _Save File_ and then save the G-code file to a location file of your choice.



## Slicing in Cura

### Opening a Model

Now we will actually slice the model we downloaded earlier. First, click the folder icon _Open File_ in the top left of the window. Then navigate to the _.STL_ file you downloaded earlier and press _Open._ You should then see the model appear on your build plate.



In order to better view your model you can right click and drag in order to change the orientation of your model. Shift + Left Click and dragging will allow you to move the position of the camera. You can always home your view with the buttons in the top-left corner. In the image above I imported three different models.

### Positioning the Model

Use the b~~u~~ttons on the left of the window in order to orient and position the parts as you want. Make sure to keep appropriate distance between parts. Make sure that the parts also have a sufficient flat surface of their model to adhere to the print bed. Check out the images below for more guidance on part orientation.

This is a good print layout

Make sure the models are kept apart

Make sure the model is correctly oriented on the print bed

### Configuring Print Settings

Next, we will configure the print settings in Cura. This will all take place on the right side of the Cura window. In a tab called _Custom._

{% hint style="info" %}
If you can't see any of the option in the steps below. Go to _Preferences &gt; Configure Cura &gt; Settings_ and change the _Setting Visibility_ to _Basic._ This will allow you to see more settings. Eventually, you can change this to _Advanced_ or _Expert_ in order to allow for more print setting options.

\_\_ \_\_
{% endhint %}

The only thing you should have to configure for your first print is the _Material: Temperature Setting._ Configure this based on the material you are printing with. If you are printing with ABS-R, I recommend a temperature of 235°C and if you are printing with PLA a temperature of 205°C is fit. Fill this into the box as shown below. For my print, I am printing with ABS-R, so I filled in 235°C.



Now we are ready to slice the model. Just click Prepare in the bottom right corner. It might take a few seconds for Cura to slice the model. Click once and wait for a few seconds.



Once you have sliced the model press the _Save to File_ button. Then save the file to a location that you will remember. You will notice that the file you are saving is a _.gcode_ file which is ready to print.

You are now ready to continue on to the next guide.

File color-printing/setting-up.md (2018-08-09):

# Setting Up

In order to print with the QuadFusion you'll need a plugin on Cura called MELT. MELT is helpful for individual layer color printing and gradient printing. This guide will assume you have already installed Cura.

**Instructions for downloading MELT:**

Go to: [https://github.com/gargansa/MELT](https://github.com/gargansa/MELT)  
Click “Download Zip”



Once you have downloaded the Zip file, go to your Local Disk → Program Files → Ultimaker Cura 3.3 → Plugins → Post Processing Plugin → Scripts

Once in Scripts, copy the MELT.py file, from when you downloaded MELT, into this folder. You should now be able to use MELT when using Cura



You can check to see if this plugin is now in Cura by opening a new Cura page and looking under Extensions --&gt; Post Processing --&gt; Modify G-Code

https://www.thingiverse.com/thing:651015/files

Next, look under the drop down tab and see if "Multi-Extruder Layering Tool 3.4.0 \(MELT\)" is there.



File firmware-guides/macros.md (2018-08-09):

# Macros

The QuadFusion has an input of four filaments and the ability to mix those filaments. This ability comes with a need to define the tools you wish to use for certain parts of your print. The purpose of defining these tools is if you have a predetermined ratio of these four filament that will create a desired color.

The Macros come into play when you want to define these tools. You can create a Macro in the Duet Web Control:





Since the QuadFusion can mix any colors you want, it is recommended that you write your own Macro. This way you can customize the colors mix ratios to suit your preferences.

The way you create a tool is the same as making one in your config.g \(Check that out in the [Tool Definitions](../printing-guides/tool-definitions.md) guide!\)

Type in a `M563` command and add a `M567` command to define the mix ratio you want for this particular tool.

This example is of a Brick Tile

Now that you have a new Macro filled with all the tools for a specific print, you can use it!

You should see your newly made Macro listed in the Macros Directory.



If you click your Macro's title you will be able to enable it.



Enable the Macro you have created. You should see that your tool settings have changed to suit the Macro you have just enabled.

If you wish to test to see if your Macro is enabled, go to the G-Code Console section and type in:  
`M567 P0`



You will be able to see the mix ratio you have designated Tool 0 to have

The purpose of doing this is if you have a specific print that requires different colors with specific tools, you can create these tools in a Macro and when you're printing the printer will have the proper tools with the proper mix ratios.

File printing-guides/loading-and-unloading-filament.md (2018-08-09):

---
description: How to load and unload filament into the extruder.
---

# Loading and Unloading Filament

## **Loading Filament**

Once the nozzle has heated up to your desired temperature you can begin loading filament.

{% hint style="info" %}
A helpful tip to loading filament is to cut the filament at a slight angle. This makes it easier for the gears inside the QuadFusion to latch on to the filament.
{% endhint %}

Starting with Tool 0, select 20mm of filament, over a period of 1mm/sec, and then click “Extrude”.



{% hint style="warning" %}
We do not recommend loading filament faster than 1mm/sec. Loading filament quickly has been known to cause grinding and skipping.
{% endhint %}

Place your index finger and thumb around the filament your are loading. You should begin feeling the filament being tugged into the Quad Head, repeat this action with the remaining filaments.



{% hint style="info" %}
If you do not feel the slight tug of the filament being pulled into your QuadFusion, check the Troubleshooting the Extruder guide for help.
{% endhint %}

Once all four filaments have been partially loaded into the QuadFusion, you can begin to load them each 20mm at a time until you see filament coming out of the nozzle.

{% hint style="info" %}
We recommend that you create a new tool that controls all the filaments, to find out how to do this go to the Tool Definitions guide.
{% endhint %}

## Unloading Filament

When unloading filament you will need to keep the nozzle heated. The purpose of this is to make sure when you are unloading the filament that it doesn't break when retracting.

Furthermore, since your filament has already passed through your QuadFusion the gears have already made a track in the filament. This means that you are able to retract the filament at a faster pace.

Thus, when retracting filament, you will want to select whichever tool you wish to start with, choose 50mm, at a pace of 15mm/sec, and click "Retract"



The filament should begin to retract at a quick pace. Repeat the same action with all the other filaments until they are completely out of the QuadFusion.

{% hint style="warning" %}
Do not pull the filament out unless it is stuck. Pulling on the filament can cause it to break which may lead to a jammed QuadFusion.
{% endhint %}

{% hint style="info" %}
If the filament is not retracting, go to the Troubleshooting the Extruder guide for help.
{% endhint %}

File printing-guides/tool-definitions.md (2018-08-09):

# Tool Definitions

This guide will explains the default tool definitions for the QuadFusion and explains how to change tools. This can be useful to create complex mixing and switching prints. This guide is not for beginners

## Default Tool Definitions

QuadFusion Tools:

* `T0`: Top Left
  * Extruder Drive 0 
  * Heater 1
* `T1`: Bottom Left
  * Extruder Drive 1
  * Heater 1
* `T2`: Bottom Right
  * Extruder Drive 2
  * Heater 1
* `T3`: Top Right 
  * Extruder Drive 3
  * Heater 1



As seen above, the QuadFusion has four different extruder drives and two heaters. The current configuration is set-up to make all tools heated by Heater 1, while the Bed will be heated by Heater 0.

## Tool Definition Command `M563`

The `M563` command allows you to define a tool, it has the following parameters:

* `Pnnn` : The tool number
* `S"toolname"`: The tool name
* `Dnnn` : The assigned extruder drive
* `Hnnn` : The assigned heater number
* `Fnnn` : The fans mapped to the tool.

The extruder drive numbers start from 0 and immediately follow the X, Y and Z axes stepper motor drives on the Duet Board. You can configure the order of these drives with the `M584` command. If you were looking at your tools in the config.g, they would look like this:



## Defining Your Own Tools

Defining your own tools is useful to create prints that switch colors in the middle of a print. To define a new tool enter the `M563` command in the configuration file, then follow it with the extruder drive and heater number that you would like to use. Such as:



## Mixing Ratios

To enable mixing rations for ta specific tool. Enter the `M568` command with the tool number \(`Pnnn` \) and the enable parameter \(`Snnn` \). For example, if I wanted to enable tool mixing for tool 3 I would enter the command `M568 P3 S1` .

To configure the actual tool mixing ratio, use the `M567` command. This will tell the firmware to use one stepper motor drive to move more than the other one when handling an extruder move. `M567 Pnnn Emmm:kkk:llll:iii` where `nnn` represents the tool number. And the rest of the letters the tool ratios of the specific extruder drives. The total of the `mmm, kkk, llll and iii` parameters should add up to 1 in order to produce a normal and expected extrusion flow rate.

## Additional Resources

* [Duet 3D Wiki `M563` ](https://duet3d.dozuki.com/Wiki/Gcode#Section_M563_Define_or_remove_a_tool)
* [Duet 3D Wiki `M567`](https://duet3d.dozuki.com/Wiki/Gcode#Section_M567_Set_tool_mix_ratios) 
* [Duet 3D Wiki `M568`](https://duet3d.dozuki.com/Wiki/Gcode#Section_M568_Turn_off_on_tool_mix_ratios)

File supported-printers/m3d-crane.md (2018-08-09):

# M3D Crane

This guide will go through the process of hooking up your QuadFusion to M3D's Crane 3D printer.

## Mechanically



**You will need...**  
**-** 3mm Hex Standoffs \(\_\_\_\_mm long\) \(x2\)

**Tools...**  
**-** 2.0mm Hex Screwdriver  
**-** 3.0mm Hex Screwdriver  
**-** Pliers

If you look behind your Crane, you should see the mount that is already fixated upon it:



Undo the circled wheel using the 3.0mm Hex Screwdriver and the Pliers



Once you have removed the bottom wheel, unscrew the two circled screws on the back of the mount.

Next, attach the two standoffs to the QuadFusion:



Finally, thread the 2.0mm Hex Screws into the standoffs, and mount the QuadFusion head onto the Crane.

## Electrically

**You will need...  
-** 24V Power Supply  
**-** Duet Maestro Board  
**-** Duet Maestro Expansion Board  
**-** Jumper

**Tools  
-** Flat-Head Screwdriver

This is the Duet Maestro:

https://duet3d.dozuki.com/Wiki/Duet\_2\_Maestro\_Hardware\_Overview

This will be a walk through on how we hooked up the QuadFusion, as well as part of the Crane, to the Duet Maestro board.

Before you can begin to wire your QuadFusion to the Duet Maestro board you must attach an extension to the board. With this extension you will be able to connect the the extra motor wires to the board.

The following pictures show where the extension goes, and how it looks once it has been plugged in:





### Base Connections



Without the fans, the QuadFusion has six main wires coming from it. The four wires with yellow dots at the ends are the motor wires. The wire with a green dot is the heater wire, and lastly the wire with the red dot is the PT1000 \(or thermistor\).

The wires plug in to their corresponding color that is boxed in the following picture:



Notes:

* Keep in mind when you're wiring your QuadFusion's motors to the Duet Maestro board which motor is connected to which port. The first picture in this guide labels each port as E0 Stepper, E1 Stepper, E2 External Driver, and E3 External Driver. When facing the front of your QuadFusion, the front left motor is 0, the front right motor is 2, the back left motor is 1, and the back right motor is 3. 
* If you decide to extend the wires given to you, make sure that you are maintaining the original positive and negative wires.

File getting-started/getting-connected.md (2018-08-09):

# Getting Connected

Overall, there are three main things you must complete in order to use your QuadFusion:

**Step One:**

You must mount your QuadFusion to whatever printer you are using. Depending on the printer you have, you may need to design a mount for your QuadFusion. 

**Step Two:**

The base QuadFusion has six connections that need to be made. Four of the connectors \(yellow\) are for each of the motors that move gears inside the QuadFusion in order to feed filament. The red wire \(green\) on the QuadFusion is the heater wire, and the white wire \(red\) is the thermistor. 



**Step Three:**

Lastly, you will need to update your firmware settings  
Go to these guides for more information about updating your firmware: [Updating Firmware](updating-firmware.md) and [Updating your Control Board Settings](updating-control-board-settings.md)

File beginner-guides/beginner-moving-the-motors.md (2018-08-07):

---
description: Beginner guide focusing on moving the motors.
---

# Beginner: Moving the Motors

Before you power on your motors you can manually move the extruder head around the printer. Follow the steps below in order to start moving the printer.

1. Move the extruder head to the center of the printer by hand. This should not take a lot of effort to do as long as the motors are not powered. Once you move the motors, the motors will be powered and resist any force acted on them.
2. Go to the _Machine Control_ tab of the Duet Web Console.

Machine Control Tab in Duet Web Console

1. Press _Home All_, this will home all the axes of the printer and ensure that the origin of the printer is located at the front-left corner of the 3D printer. After the homing process is complete, you can see that the position of the 3D printer is updated in the _Machine Status_ tab on the Duet Web Console.
2. Press the X-10 button in the _Head Movement_ window. This will move the extruder carriage of the printer 10mm in the negative X direction, this should be towards the left if you are facing the front of the printer. Now press the Y-10 button, this will move the printer -10 mm in the Y-direction. If you are facing the front of the printer, this should send the bed carriage away you.  Press the Z-10 button in order to move the extruder down 10 mm.
3. You can keep pressing the buttons to move the extruder carriage to become more familiar with the directions and coordinate system of the Crane.

**Absolute vs. Relative**

A 3D printer movement allows for two different modes, absolute and relative. These two terms are also used frequently in machining and other engineering processes. Absolute describes a position or command with respect to the origin or zero position. Remember that for the Crane the origin is located in the top-left-front corner. Relative describes the position of a 3D printer relative to the previous point the printer was located at. For example, if you tell the printer to move \(20,20,20\). Absolute mode will send the printer to the point where X = 20mm, Y = 20mm and Z = 20mm, relative to the origin. While relative will send the printer 20 mm in the X-direction, Y-direction and Z-direction relative to its previous position. This means your printer will go to two completely different places depending on if you are in relative or absolute mode.

If you were to tell the printer to go to \(20,20,20\) while the printer was in absolute mode, it would result in the printer first moving to \(20,20,20\). If you told it again to go to \(20,20,20\) it would just stay there. The Duet would say: I am already there! If you told the printer to move \(20,20,20\) twice while the printer was in relative mode. The printer would move 20mm in the X, Y and Z directions the first time. And then move 20mm in the X, Y and Z directions for the second time as well. This is the difference between absolute and relative.

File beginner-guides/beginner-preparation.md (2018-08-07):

---
description: 'Start of the beginner guides, complete these steps before continuing.'
---

# Beginner: Preparation

Before starting the Beginner Guides guides, please complete the following steps to ensure your printer is working properly and is connected to your local network.

1. Read the [Critical Warnings](../getting-started/critical-warnings-and-information.md) in the Getting Started chapter of the QuadFusion. This contains useful and important information about what to do and \(more importantly\) what not to do with your QuadFusion.
2. Follow the [Unboxing & Assembly](https://quadfusion.printm3d.com/~/edit/drafts/-LIRqdq5PX_HDBbChvND/getting-started/accessing-your-sd-card) and [Getting Started ](https://quadfusion.printm3d.com/~/edit/drafts/-LIRqdq5PX_HDBbChvND/getting-started)guides. This will make sure your QuadFusion 3D Print Head is ready to undergo the rigorous Beginners Guide.
3. Continue on to the next guide!

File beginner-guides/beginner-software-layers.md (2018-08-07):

---
description: A guide covering the different software layers of the Crane.
---

# Beginner: Software Layers

This guide is intended to explain all the different software levels that takes a model to a final printed form on the Crane. We will start at a model on a modelling software on a computer and go all the way down to the RepRap firmware that runs on the Duet Maestro.

## Software Layers

| Layer | Purpose |
| :--- | :--- |
| Model Software | Create _.STL_ models of prints |
| Slicing Software | Convert _.STL_ files to ._gcode_ files while incorporating printer and print settings |
| Duet Web Interface | A web server running on the Duet Maestro that connects to your local network in order to allow for control and monitor of a 3D printer |
| Configuration Settings | G-code files on the microSD card which are loaded upon the boot-up of the Duet board in order to properly configure the board for the printer |
| Firmware | Software running on the Duet Maestro that handles G-code and other operations. Can not be configured. |

## Model Software

If you want to print something on a Crane you will first have to create or find a model of what you plan to print. Creating and designing a model is currently done with CAD \(Computer Aided Design\) software such as SolidWorks or TinkerCAD. SolidWorks offers a more technical and precise solution to designing models, while TinkerCAD represents an easier and faster solution. Aside from creating your own models you can find many models online. These models exist on websites such as [Thingiverse](https://www.thingiverse.com/), [Pinshape,](https://pinshape.com/) [MyMiniFactory](https://www.myminifactory.com/) and many others! In the next step you will see that you need slicing software and slicing software will require a specific file type. That file type is called a ._STL_ file or [stereolithography](https://en.wikipedia.org/wiki/STL_%28file_format%29) file. This file type stores the outside shell of a model, which is typically all the slicer needs. Whenever you design or find a model to print it you will have to convert it to a ._STL_ file in order to slice it.

## Slicing Software

Slicer software fills the void between the model and the 3D printer. The 3D printer can only understand G-code commands and the modeling software can only generate models. Slicer software allows you to convert a model to G-code that will allow a 3D printer to create a print. Incorporated into the slicer software are many different print and printer settings. Print settings refer to the things such as extrusion, cooling and print temperature. Printer settings configure things such as the build volume of the printer or the starting and ending G-code for a print. This software is called a slicer as it typically converts a model into many different layers to print one at a time. The slicing software creates a file type called a _.gcode_ file. This is a long list of commands that can be interpreted by the Duet Board. The G-code commands in this file are exactly the same as the ones you would enter in manually, such as `G1` , but just in a long list.

## Duet Web Interface

To allow control of the Crane you have the Duet Web Console. This is a simple web server that runs on the Duet Maestro and connects to your local network. Aside from control the Duet Web Console allow you to observe various different statistics, status tables and values of the Crane. This allows you to troubleshoot problems much easier with more feedback. You can start and end prints from here. The Duet Web Console also allows you to configure certain settings on the Crane.

## Configuration Settings

The SD card stores files that allow for the operation of the Duet Web Server as well as configure the board, the settings that configure the board can be referred to as the configuration settings. The microSD card has four different folders that each handle a certain part of the Duet board operation \(look in [SD Card Structure](https://m3d.gitbook.io/promega-docs/getting-started/sd-card-structure)\). The SD card files operate on a higher level. The files located in the _sys/_ folder, configure the board. They can be changed by the user at any time, either through the Duet Web Console or by changing the files from your computer. The configuration files often simply represent a grouping of G-code commands that are run upon the boot of the Duet board. Whenever the Duet Board is booted up, it will have no settings loaded. So whenever _config.g_ is run on the start, it gets configured with the settings inside. These configuration files are in the form of G-code files. When you download the SD card file from the M3D Github Repository, you are just taking the M3D preferred settings for the Crane.

## Firmware

The firmware on the board is a version of RepRap released by DC42. The firmware is released on his [GitHub Releases](https://github.com/dc42/RepRapFirmware/releases). If you want to update your firmware, you can follow the [Updating Firmware](https://m3d.gitbook.io/promega-docs/firmware-guides/updating-firmware) guide. The RepRap firmware on the board interprets all the G-code commands sent to the board. It is stored on the micro-processor on the Duet Maestro and required for the board to operate. The firmware handles low-level operation such as controlling the stepper motor drivers or processing G-code commands. Changing the firmware directly is not possible, you will have to update the firmware using the guide above.

The next guide: [What is Slicing?](beginner-what-is-slicing.md) will cover how slicing works and helps you configure your slicer.

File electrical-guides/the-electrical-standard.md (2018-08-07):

---
description: An explanation behind the wiring of the Crane.
---

# The Electrical Standard

This guide serves to describe the standard for the electrical system of the QuadFusion and the reasoning behind it.

## The Standard

For all the electrical components of the QuadFusion, when facing the front \(from left to right\) the motors \(or filament entry points\) are Drive 1, Drive 0, Drive 3, and Drive 2. 

## Reasoning

The Duet board features two different ports for the extruders, thermistors and heaters. Additionally, the extruder assembly wiring features different connectors for all of these components. On top of that, you can configure the software settings of each of the tools in order to use particular heaters or extruders. This all combined allows you to create a large number of configurations for the extruder wiring. This standard is meant to explain and standardize that wiring.

## Explanation

### Extruder Drives

The Duet Maestro board has two different ports for the extruder, often referred to as E0 and E1. With this standard, the E0 port will power Drive 0 and E1 will power Drive 1, always. Additionally, with the extension board added, External Driver 2 will power Drive 2 and External Driver 3 will power Drive 3, always. 

### Heaters

The Duet Maestro has two different heater ports labeled E0 HEAT and E1 HEAT. These are also noted as H1 and H2, because the heated bed is H0. With the standard, H1 will correspond to the extruder's heater and H2 will not be bothered.

## Thermistor

The thermistor's ports on the Duet Maestro are referred to as E0 TEMP and E1 TEMP. In the firmware of the Duet, E0 TEMP is always bound to E0 HEAT and E1 TEMP is bound to E1 HEAT. Therefore, E0 TEMP corresponds to the bed heater and E1 TEMP corresponds to the extruder heater.

## Tools

The QuadFusion has a minimum of four tools, thus the drives previously mentioned will correspond to the tools. Such as, Drive 0 will be Tool 0, Drive 1 will be Tool 1, and so on. 

## Deviating from the Standard

In the configuration files and the wiring of the QuadFusion you can deviate from this standard. To change the tool definition in the configuration files, read the [Help! My Extruders are Backwards](https://promega.printm3d.com/~/edit/drafts/-LHcd83qhBiRw2GAgwN_/firmware-guides/help-my-extruders-are-backwards) guide. For wiring read [Duet Maestro Wiring](https://promega.printm3d.com/~/edit/drafts/-LHcd83qhBiRw2GAgwN_/electrical-guides/duet-maestro-wiring) and [Extruder Assembly Wiring](https://promega.printm3d.com/~/edit/drafts/-LHcd83qhBiRw2GAgwN_/electrical-guides/extruder-assembly-wiring).

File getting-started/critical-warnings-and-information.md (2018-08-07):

# Critical Warnings & Information

The M3D QuadFusion 3D Print Head is an industrial product. The user assumes all responsibility for proper operation and acknowledges that they understand the operation and standard practices of additive manufacturing. The user assumes all responsibility for its proper use and agrees to follow the directives below to ensure a safe and working unit before any other operation.

## Warnings

1. DO NOT TOUCH PRINT HEAD WHILE OPERATING The QuadFusion is a powerful industrial machine. While the QuadFusion is moving or printing you should not reach into the buildspace.
2. USE UNDER SUPERVISION

   Place the printer in a place where nothing can catch on fire should the worst occur. The QuadFusion 3D Print Head is constructed out of metal and fireproof materials. Still, PLA and other filaments can burn and cause a fire if the print head is used improperly.

3. MAXIMUM EXTRUDER SPEED

   Don't extrude faster than 5.6 mm^3/s with any filament in extruder to start. Get success first with no skipping then try to push the limits. Do the math: 45mm/s movement, 0.3 mm layers and 0.5 mm wide would be 6.75mm^3/s , a bit to fast for your first print, especially with pla. So adjust layer heights accordingly, for example to 0.25mm high for your first prints. Over time you should be able to print faster. Remember that speed depends on material, number of print moves per second, nozzle type and temperature.

4. BURN HAZARD

   NOZZLES may cause burns when hot.

5. WATCH THE FAN

   The cold section fan is spinning very fast when the system is on. Please keep tools and yourself clear of it when it is operational.

## Next up

1. Continue on to the [Unboxing & Assembly](https://m3d.gitbook.io/promega-docs/getting-started/unboxing-and-assembly), the next chapter in the [Getting Started](https://m3d.gitbook.io/promega-docs/getting-started) guide.

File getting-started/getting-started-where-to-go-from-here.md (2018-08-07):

---
description: What now?
---

# Getting Started: Where to Go From Here

Now that you have completed the Getting Started guides. You are ready to go. Consider reading the following guides as you learn more about the QuadFusion and its functionalities.

* [Supported Printers](../supported-printers/): For more specific information on how to mount the QuadFusion 

  * [M3D Crane](../supported-printers/m3d-crane.md)
  * [M3D ProMega](../supported-printers/m3d-promega.md)
  * [CR-10S](../supported-printers/cr-10s.md)
  * [Prusa i3 MK2S](../supported-printers/prusa-i3-mk2s.md)

* [Duet3D G-code Wiki](https://duet3d.dozuki.com/Wiki/Gcode): All supported G-code commands
* [Duet Maestro Wiring](https://promega.printm3d.com/~/edit/drafts/-LHJUCJ_8YzW4nrKjE3M/electrical-guides/duet-maestro-wiring): Explanation on just wiring the Duet Maestro Board.
* [Macros](https://promega.printm3d.com/~/edit/drafts/-LHJUCJ_8YzW4nrKjE3M/firmware-guides/macros): Learn more about macro files and how they can make your life easier.
* [Repair Guides](https://promega.printm3d.com/~/edit/drafts/-LHJUCJ_8YzW4nrKjE3M/repair-guides): The chapter that can fix all your problems \(hopefully\).
* [Maintenance Guides](https://promega.printm3d.com/~/edit/drafts/-LHJUCJ_8YzW4nrKjE3M/maintenance-guides): Maintain the printer!

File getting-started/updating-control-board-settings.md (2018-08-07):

---
description: Update the contents of the Duet Maestro microSD card.
---

# Updating your Control Board Settings

The QuadFusion requires printer electronics capable of running four independent extruder motor channels, either natively via the printer's control board or with an attached expansion board.

If you are running your QuadFusion from a Duet 2 Maestro plus Extruder Expansion Board, configuration files are available for several printers on which we've tested the Quad Fusion.  These files can be found in [GitHub](https://github.com/PrintM3D/QuadFusion).  Be careful when first using these files!  While they have common settings for printer geometry, end stops, etc. these settings may not correspond to your printer exactly, and using the files without reviewing the settings could damage your printer or the QuadFusion head.  For a walk through on adjusting necessary settings before running your printer, see our [Firmware Guides](https://quadfusion.printm3d.com/firmware-guides).

If you are setting up a Duet 2 Maestro manually or running your QuadFusion from alternate electronics, here are the basics of the QuadFusion design you'll need to get up and running:

* Motor current: 500 mA peak The motors are designed for the best combination of extrusion force and thermal performance when operating in the range 480 - 525 mA.  We suggest setting your extruder motor current \(all four channels!\) at 500 mA as a starting point.  Do not run your motors above 525 mA as they will self-heat and can cause damage to themselves or the rest of your printer. 
* Extruder steps per millimeter: 984 microsteps/mm at a microstep setting of 8x We recommend getting started at 8x microstepping.  Higher microstepping can offer some benefits to print quality when mixing at disparate ratios, but may present difficulty for control boards with low maximum step rates.  For more information on the step rates achievable on various electronics, see [this article](https://reprap.org/wiki/Step_rates) on the RepRap wiki. 
* Temperature sensor: PT1000, resistance at room temperature is 1050 Ω In addition, if you are setting up the QuadFusion on a Duet 2 Maestro, note that the series resistance \(of voltage divider feeding the chip's ADC for temperature reading purposes\) is 2200 Ω.

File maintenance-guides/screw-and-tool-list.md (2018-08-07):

# What You'll Need

This guide contains a list of different screws and tools used for each assembly of the QuadFusion and its fans. Look under the tool's header for each assembly to see all the possible tools you will need to maintain, assemble or repair the QuadFusion or its fans . Look under the screws category to view a more in-depth list of the screw types and their location.

## Brief Overview

### All Tools

* T-10 Torx Screwdriver
* T-6 Torx Screwdriver
* 2.5 mm Hex
* 1.3 mm Hex
* Pliers
* Needle-nose pliers

### All Screws

* Hot-end Block Set screws: 1.3 mm Hex
* Fan mount: T-10 Torx
* Fan Duct: T-6 Torx
* QuadFusion: T-10 Torx and 2.5 mm Hex\*
  * \*The 2.5mm Hex screw may vary based on how you are mounting your QuadFusion. Go to the [Mounting the Hardware]() guide for more information. 

## Detailed List

### QuadFusion Assembly

**Tools**

* T-10 Torx
* 2.5 mm Hex

**Screws**

**2.5 mm Hex:**

* Mounting Quad \(bottom\)

**T-10 Torx:**

* Mounting Quad \(top\)
* Nozzle Screw

### Hot-end Assembly

#### Tools

* 1.3 mm Hex
* Pliers

#### Screws

**1.3 mm Hex**:

* PT1000 Setscrew
* Heater Cartridge Setscrew
* Nozzle Setscrew

### Fan Mount Assembly

**Tools**

* T-10 Torx
* T-6 Torx

**Screws**

**T-10 Torx:**

* Fan Mounts

**T-6 Torx:**

* Fan Ducts

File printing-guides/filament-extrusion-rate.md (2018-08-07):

# Filament Extrusion Rate

The extrusion system on the QuadFusion is designed to print at specific speeds at certain temperatures. Printing at the proper filament extrusion rate is essential to provide a good print. The QuadFusion is designed to extrude at a rate of 5.7 mm^3/s. This number can change significantly depending on your printer and slicer settings and material.

## Calculating Filament Flow Rate

Calculating the flow rate of your extruder is typically very easy. The equations you can use to calculate filament flow rate depends on your print settings and whether you are printing or not. Follow the _Extruding in Air_ section to calculate the flow rate while extruding filament in the air and the _Printing Flow Rate_ section in order to find the filament flow rate while printing.

### Extruding in Air

When the extruder is printing filament into air, we can assume that the extruder is creating a steady stream of filament at a slightly larger diameter than the diameter of the nozzle. If the extruder is not skipping, you can use the feedrate of the extruder move and the cross-section of the filament to calculate the flow rate. Because, all the filament that is being pushed by the extruder is pushed through the nozzle. Follow the equation below:

_Flow Rate \(mm^3/s\) = Feedrate \(mm/s\)_ \(Filament Cross-section\) \(mm^2\)\*

_Filament Cross-section = pi_ \(\(Filament Diameter\) / 2\)^2 \_\_Filament Cross-section for 1.75mm filament: 2.405 mm^2\*

**For Example:** You send the command `G1 E100 F200`, where you extrude 100mm of filament at 200 mm/min. You are using 1.75 mm filament.

_Flow Rate = 8 mm/s = pi_ \(1.75 / 2\)^2 _\(200 / 60\) = 2.405_ 3.333\*

Remember that the `G1` move command feedrate parameter, `F`, uses mm per minute. So divide the feedrate by 60 to obtain the feedrate in mm per second.

### Printing Flow Rate

When printing, the flow rate depends on your layer height, nozzle diameter and print speed.

_Flow Rate \(mm^3/s\) = \(Extrusion Width\)\(mm\)_ \(Layer Height\)\(mm\) _Print Speed \(mm/s\)_ _Extrusion Width is ~120% of nozzle diameter_

**For Example:** You have a 0.5 mm nozzle mounted and you are printing at 0.25mm layer height at a print speed of 30 mm/s.

_Extrusion Width = 0.6 mm = 1.2_ 0.5 _Flow Rate = 4.5 mm^3/s = 0.6_ 0.25 \* 30

## QuadFusion Flow Rate

The QuadFusion is designed to extrude filament at 5.7 mm^3/s. If you find your extruder skipping or notice print quality problems, do a filament flow calculation to determine the extrusion rate you are printing at. The extrusion rate of the QuadFusion can be increased significantly depending on material, printing temperature and other factors. Feel free to experiment and push the extruder to its limits! But remember to calculate the filament flow rate to determine whether your goal is realistic.

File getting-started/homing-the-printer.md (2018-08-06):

---
description: How to home the Crane.
---

# Changing Homing Offsets

More details coming soon.

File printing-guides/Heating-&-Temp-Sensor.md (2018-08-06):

---
description: Getting the heater and Temp sensor calibrated on the QuadFusion 3D Print Head.
---

# \*Heating & Temp Sensor

This guide expects the reader to have completed setting up its QuadFusion, all except the Heater. Your printer should be homed, the fans should be mounted, and the QuadFusion should be correctly assembled. 

1. Connect to the Duet Web Control
2. Go to Settings, and under System Editor you will want to open up your printer's config.g .
3. Scroll until you have reached the Heater section. Which may look like what's below:

`;Heaters                                                                               M305 P0 T100000 B4138 C0 R2200   ;Set thermistor+ADC parameters for heater 0            M143 H0 S120                     ;Set temperature limit for heater 0 to 120C                            M305 P1 X501 T1050 R2200         ;Set themistor+ADC parameters for heater 1                 M143 H1 S280                     ;Set temperature limit for heater 1 to 280C` 

`M305` Explained:

`M305` is the G-code command that sets the heater's parameters by using \(as above\)  
`Pnnn` is used to describe which heater is being edited  
`Xnnn` is the heater ADC channel, or thermocouple or PT100 adapter channel  
`Tnnn` is used to indicate the thermistor's resistance   
`Bnnn` is the beta value if the sensor is a thermistor  
`Cnnn` is the Steinhart - Hart C coefficient \(default 0\)  
`Rnnn` is the series resistor value for the PT1000 and PT100

`M143` Explained:

`M143` is   
`H` is the heater being edited  
`S` is the maximum temperature

{% hint style="info" %}
All this information can be found at: [https://duet3d.dozuki.com/Wiki/Gcode\#Section\_Introduction](https://duet3d.dozuki.com/Wiki/Gcode#Section_Introduction)
{% endhint %}

4. Try heating up your tools to 200C. You should see the red line on the graph begin to increase:



Additionally, you should see that the Current temperature matches the Active temperature. This indicates that you thermistor \(PT1000\) is working as well. 



If anything is wrong, or you received a Heater Fault, go to the [Heater Troubleshooting](../troubleshooting-guides/heater-troubleshooting.md) guide for help.

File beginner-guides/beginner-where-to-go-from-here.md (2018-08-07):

# Beginner: Where to Go From Here

Now that you have completed the beginner guides you can continue to the following guides:

* Browse the [Getting Started](../getting-started/) chapter to ensure you know everything

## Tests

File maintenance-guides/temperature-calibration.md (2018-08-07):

# Temperature Calibration

Proper temperature calibration is vital to allow for good print quality. The hot-end and the bed are controlled by temperature feedback loops which are supposed to maintain a steady temperature. The type of feedback loop is a first order plus dead time \([FOPDT](https://controlguru.com/process-data-dynamic-modeling-and-a-recipe-for-profitable-control/)\) loop. This loop has three different control variables: 1. Gain: Kp: Allows for manipulation of the strength of the heater response. 2. Time Constant: Tp: Control of the speed of the response of the heater. 3. Dead time: The delay before the system will begin a response.

This control loop and its variables are applied to the different heaters on the Crane. With the command `M303` and `M307` the temperature control loop can be tuned and changed. The default control variables supplied by M3D in the configuration files should allow you to print at a stable temperature. However, significant changes to the printing environment, such as room temperature, air-flow or humidity can impact your control loop effectiveness and stability. An improper control loop can cause problems listed below.

* **Overshoot**: A response to a new set-point will send the temperature of the heater significantly beyond the set-point. An overshoot of about 15°C is reasonable. A greater overshoot can cause your filament to char or present a fire hazard. 
* **Oscillation**: An unstable control loop can result in a temperature oscillation. An oscillation of more than 5 °C degrees can impact printing quality.
* **Steady-state Error**: The stable temperature output of the control loop does not reflect the temperature set-point.
* **Long Response Timer**: The heater will take a long time to achieve the desired set-point. While not dangerous, this can be an annoying and unnecessary delay.

## Auto-tuning

RepRap firmware has a built in auto-tune heater function. This allows you to tune the control loop of a heater on the Crane. Follow the section below!

{% hint style="warning" %}
**The auto-tune function can rapidly heat your hot-end\(s\) to a high temperature. DO NOT leave your printer unattended while running** `M303`
{% endhint %}

**Overview**

The command `M303` will heat-up your hot-end to a set-point temperature and record data as it does so. Therefore, while your hot-end is undergoing it is important to replicate the conditions that your 3D printer prints in. For example, turning on your nozzle fans. First, the tuning process will heat the hot-end to your set temperature. It will likely overshoot the set-point. The nozzle will then cool-down to room temperature. If you instructed the control board to perform multiple cycles, it will repeat this process multiple times. Once complete, the firmware will return suggested control variable values.

`M303` Parameters:

* `Hnnn`: Heater number \(by default: 0 is bed, 1 & 2 hot-ends\)
* `Pnnn`: PWM percentage from 0 to 1.
* `Snnn`: Set-point temperature in °C

`M307` Parameters:

* `Hnnn`: Heater number \(by default: 0 is bed, 1 & 2 hot-ends\)
* `Annn`: Gain constant
* `Cnnn`: Time constant
* `Dnnn`: Dead time
* `Fnnn`: PWM frequency
* `Bn`: Bang-bang control enable \(1\)
* `Snnn`: Maximum PWM
* `Vnnn`: Vin at the time of calibration. Allows for compensation of power supply voltage variation.
* Unload the filament from your hot-end. Once you are more familiar with the `M303` command, this step is not necessary. We recommend removing filament as it can burn and char inside your hot-end if the tuning process reaches a high temperature.
* Wait for the heater to reach room temperature. **This is important to achieve a good result!**
* Send the `M303` command. Change the `H` parameter to reflect the heater number. The PWM percentage can be changed with `P` if the heater is heating up too fast, and the firmware is unable to present control variables. The `S` parameter should be set to a typical printing temperature, such as 230°C. An example would be `M303 H1 P0.5 S230` in order to run auto-tune on hot-end 1, with 50% PWM and to 230°C.
* Wait for auto-tune to complete. Do not leave the printer unattended.
* The firmware should print out the calculated control variables. Sending `M303` should also display the control variables.
* Use the `M307` command in order to set new control variables. Use the parameter list above to determine the proper syntax. 
* Remember to replace the `M307` command in the configuration file _config.g_ with the command you just entered in order for your changes to take effect upon a system restart.

## Legacy PID Control

RepRap firmware also allows for control of the heaters with basic PID with three different constants: Kp, Ki, Kd. Use the command `M301` in order to send enable and send these control variables. These control variables also can be found by running the `M303` auto-tune as listed above. The command `M301` will enable the legacy PID control loop.

`M301` Parameters:

* `Hnnn`: Heater number
* `Pnnn`: Proportional constant \(Kp\)
* `Innn`: Integral constant \(Ki\)
* `Dnnn`: Derivative constant \(Kd\)

## Manually Tuning

Manually tuning your control variables can be done. Read more about the control variables explained in this guide online and their effects on a control loop before changing your control variables. Manually tuning your control variables is often a great option to reduce or obstruct observed errors as the ones listed above. **Tuning your control loop from scratch is not recommended!** Be careful when changing your control variables as it could easily produce unintended consequences

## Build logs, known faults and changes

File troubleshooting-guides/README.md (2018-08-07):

# Troubleshooting Guides

The guides in this chapter are intended as generic troubleshooting guides for specific components or functionalities of the QuadFusion.

{% page-ref page="troubleshooting-duet-web-console.md" %}

{% page-ref page="my-drives-tools-are-backwards.md" %}

{% page-ref page="heater-troubleshooting.md" %}

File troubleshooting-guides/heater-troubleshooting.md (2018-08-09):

# Heater Troubleshooting

This guide serves to fix any problems you might have with the heater cartridge or PT1000.

## PT1000 Problems



The PT1000, or thermistor, is what reads the temperature of the heater block and relays the information onto the Duet Web Control.

### **Possible Problem\(s\):**

**Not Reading Temperature:**  
This is assuming that whenever you attempt to to heat your extruder the thermistor doesn't read any value which results in a heater fault. It is very likely that the issue here lies within your printer's settings.

**Solution:**

{% hint style="info" %}
This solution is more directed towards Crane users. If you have a different printer, you may need to tweak some things.
{% endhint %}

Go into Settings, System Editor, and under config.g go to the Heater section:

`;Heaters M305 P0 T100000 B4138 C0 R2200 ;Set thermistor+ADC parameters for heater 0 M143 H0 S120 ;Set temperature limit for heater 0 to 120C M305 P1 X501 T1050 R2200 ;Set themistor+ADC parameters for heater 1 M143 H1 S280 ;Set temperature limit for heater 1 to 280C`

Try changing the values to match what is above, look under [Heating & Temp Sensor](heater-troubleshooting.md) guide to fully understand what each letter means.

## Heater Problems

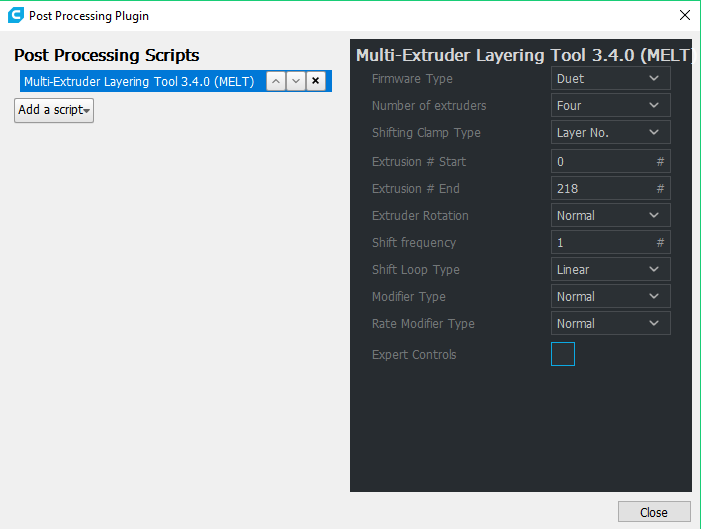
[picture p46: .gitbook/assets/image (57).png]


### Possible Problem\(s\):

**Heater Faults:**  
When trying to heat up your nozzle, if you receive a heater fault there can be a few reasons. The first possibility is that your printer's settings have been set up to expect that your heater will heat faster than it is able to. The second possibility is that your heater is not heating.

**Solution:**  
The first reason for a heater fault can be solved by editing your printer settings. Go into Settings, System Editor, and under config.g go to the Heater section:

**Loose Connection:**  
It is possible when setting up your QuadFusion that the Heater wire was bent. The pins in the connector may have gotten loose, which is causing your heater to heat poorly. You may be able to identify this issue by trying to heat your nozzle and wiggling the heater wire. If you get a similar result as the picture below, you have a loose connection:

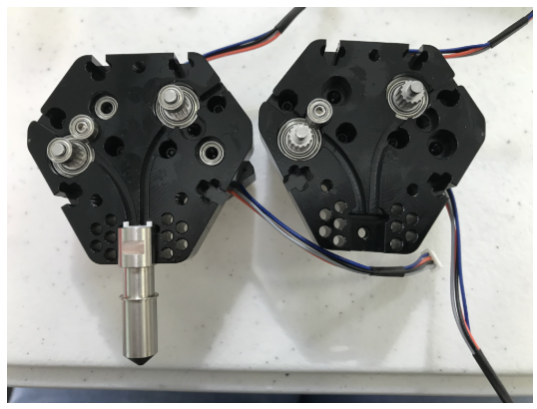
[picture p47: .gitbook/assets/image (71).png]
Image pulled from: https://forum.duet3d.com/topic/4966/highly-erratic-temperature-readings-above-certain-temperature


As you can see the red line is no longer steadily rising, but has begun to move exaggeratedly.

**Solution:**  
There are two solutions, the first being replace your heater wire entirely. Unless you have the means for the second option, this is by far the least tedious.

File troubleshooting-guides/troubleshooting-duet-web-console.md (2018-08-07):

# Troubleshooting Duet Web Console

This guide will walk through possible problems that can be encountered while connecting to the Duet Web Console.

## Rejected by the Duet

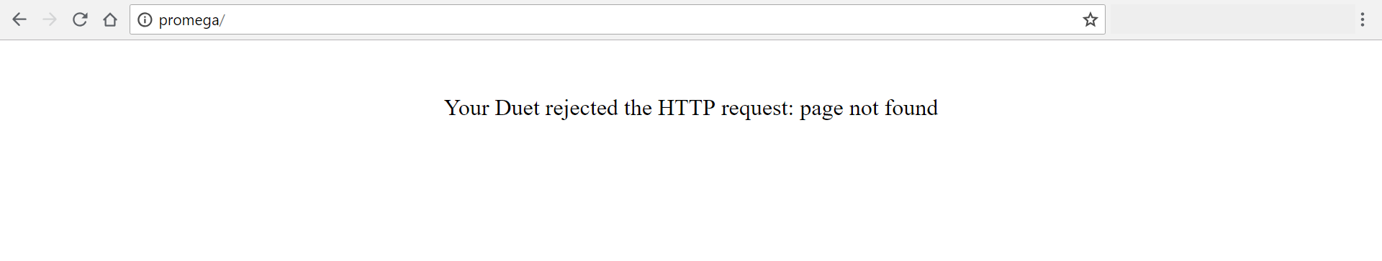
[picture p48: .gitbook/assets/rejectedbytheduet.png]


### Problem

When attempting to connect to the Crane the error "Your Duet rejected the HTTP request: page not found" is shown.

This indicates that the web pages of the Duet web server can not be loaded from the SD card. Usually the problem lies in the SD card not being properly mounted to the system. This can happen if you ejected the SD card and then put it back into the Duet board while it was powered.

### Solution

* Reboot the Duet Maestro board with the microSD card properly fitted inside.
* Reformat the microSD card.
* [Update the microSD card files.](../getting-started/updating-control-board-settings.md)
* [Update the Duet Web Firmware.](../getting-started/updating-firmware.md)

## Frequent Disconnects from the Duet Web Console

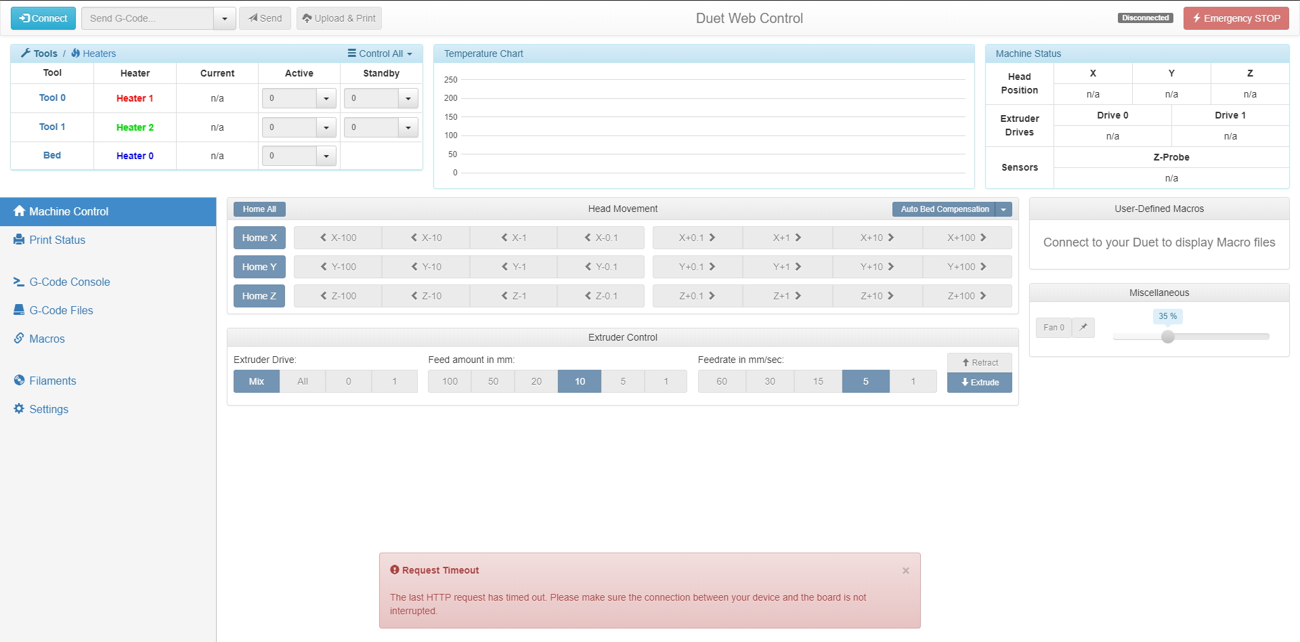
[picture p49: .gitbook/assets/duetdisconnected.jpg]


### Problem

When working with the Duet Web Console there are frequent disconnects with the Duet Web Console.

### Solutions

* Ensure that your computer has a proper connection to the local network. It is possible that the Duet is not disconnected from the network but your computer is.
* Ensure that the Duet has a proper connection to your local network.
* [Try configuring a static IP address](). It is possible that the router is continuously changing the IP address of your Crane.
* Go to _Settings &gt; General_ on the Duet Web Console and increase the _Status Update Interval_ and _Maximum Number of AJAX Retries_.

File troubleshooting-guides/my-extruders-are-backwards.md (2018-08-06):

# \*My Drives / Tools are Backwards

Whenever you are changing or updating configuration files it is possible that your drives will be wrongly configured. This could result in your extruder drivers going the wrong way, or Drive 2 spinning when you want Tool 1 to be extruding.

## Flipping Extruder Directions

This will fix extruder drives that are going backwards. For example if you pressed the button _Extrude_ on the Duet Web Console it will result in the drive pushing filament back out of the extruder hole as if you were retracting. **Heads-up read the information box below.** 

{% hint style="info" %}
It is possible that your extruder directions are flipped because the extruder drives are flipped, meaning the 4-pin Dupont connector is backwards on the Duet Board. Try flipping the connector and seeing if the issue is resolved.
{% endhint %}

1. Connect to the Crane's Duet Web Console
2. To check your extruder directions go to the _Machine Control_ tab in the Duet Web Console and select drive 0 or 1 in _Extruder Control._ Then try to feed filament into the extruder and see if your directions are correct. It is also possible to change the extruder drives in the section below. If your filament is being pushed out of the top of the extruder when you press extrude, follow the steps below.   
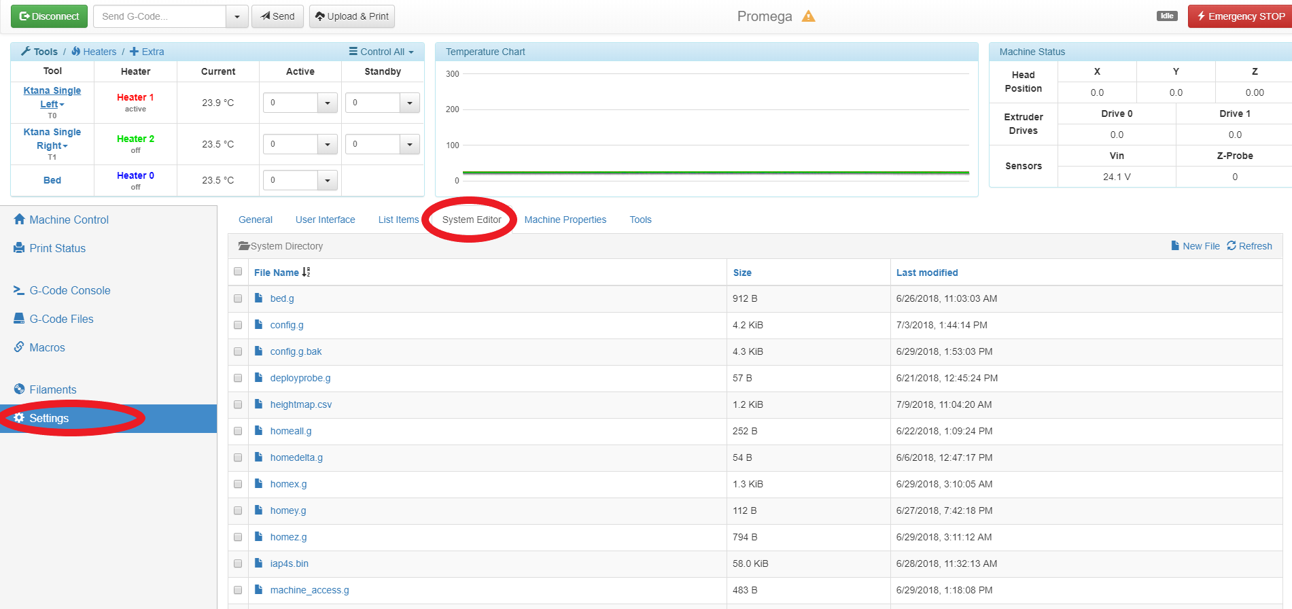
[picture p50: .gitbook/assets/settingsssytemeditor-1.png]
3. Go to the _Settings_ tab of the Duet Web Console and then to the _System Editor._   
4. Open the _config.g_ file. Find the block with the following commands: `; --- SECTION: DRIVES (MOVEMENT SECTION) ---`
5. `; Drives  M569 P0 S1 ; Drive 0 goes forwards, Tool 0   M569 P1 S0 ; Drive 1 goes backwards, Tool 1   M569 P2 S0 ; Drive 2 goes backwards, Tool 2   M569 P3 S1 ; Drive 3 goes forwards, Tool 3`  
6. Depending on which drive is going backwards change that drive's direction with the `S` parameter. For example, if Drive 3 was going backwards, I would change the command to go from `M569 P3 S1`

   to`M569 P3 S0.`

7. Save the file and reboot the system. Repeat step 2 to confirm that the directions are correct.

## Flipping Extruder Drives

This section will fix extruder drives that are flipped. If you actuate what you think is the one drive and it results in a different drive spinning. 

{% hint style="warning" %}
**The inherent problem here lies in wiring, so be aware, the fix you are applying requires the printer to be off.**
{% endhint %}

 The wiring is intended to have Drive 0 \(Tool 0\) wired to extruder drive 0, Drive 1 \(Tool 1\) to extruder drive 1, and so on. To fix this permanently fix the wiring of your QuadFusion.

1. Connect to the Printer's Duet Web Console
2. To check your extruder drives go to the _Machine Control_ tab in the Duet Web Console and select Tool 0, 1, 2, or 3 in _Extruder Control._ If you have Tool 0 selected and press extrude it should move the Drive 0. For Tool 1, Drive 1 should move.  It is also possible to change the extruder drives in the section below.
3. Now that you have pinpointed which Tools are switched, turn your printer off.

As an example, let's say that when you try to extrude Tool 1, you instead trigger Drive 3 which sends the wrong color and vice versa. To fix this all you need to do is flip the connectors for Drive 1 and Drive 3.

{% hint style="info" %}
**Remember,**  Drive 0/ Tool 0 connects to Extruder Drive 0,  Drive 1 / Tool 1 connects to Extruder Drive 1,  Drive 2 / Tool 2 connects to External Drive 2, Drive 3 / Tool 3 connects to External Drive 3 
{% endhint %}

If you are unclear which wire connects to which port, go to the [Duet Maestro Wiring](../supported-printers/duet-maestro-wiring.md) guide for help.

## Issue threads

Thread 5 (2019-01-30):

M3D Promega page update.

ericl-m3d, 2019-01-30:
Here's some background knowledge for completing the page labeled "M3D Promega" (https://quadfusion.printm3d.com/supported-printers/m3d-promega).

* There's a subassembly kit they can purchase here: https://store.printm3d.com/products/promega-quad-head-assembly-m3d0540898?variant=12397469073486

* The Quad assembly video will be housed in the Promega Gitbooks (link: https://promega.printm3d.com/m3d-community/add-ons/quad). NOTE: this link may change, will update, if so.

I think that should be minimum. Might be missing something.

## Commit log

2018-07-09 belt tensioning guide: redo formatting
2018-07-10 Replaced all images src from the old site to this repo. 👍
2018-07-10 Cleaned some links in heating the bed and nozzles
2018-07-10 Fixed links in routing Z belts
2018-07-10 Fixed links in belt tensioning
2018-07-10 Fixed links in changing extruders
2018-07-10 Updated links in Z-probe calibration
2018-07-10 Fixed links in homing macro adjustment guide
2018-07-10 Fixed extruder assembly wiring links
2018-07-10 fixed links in repairing belt clamps
2018-07-10 fixed links in unboxing and assembly
2018-07-10 fixed some more links in preparing a print
2018-07-10 fixed links in homing the printer
2018-07-10 fixed links in running-a-print
2018-07-10 fixed links in duet wiring
2018-07-10 Updated unboxing and assembly, need to add images
2018-07-17 Inserted step 23
    The Z-probe should be retracted before moving the bed to the nozzle.
2018-08-02 GitBook: [master] one page and 2 assets modified
    [quad-fan-mount-2-v1.1 (1).STL, quad-fan-mount-2-v1.1.STL]
2018-08-02 GitBook: [master] one page and one asset modified
    [quad-nozzle-fan-duct-v1.0.STL]
2019-01-24 GitBook: [master] 4 pages and one asset modified
    [cr10s_quad_stencil.stl]
